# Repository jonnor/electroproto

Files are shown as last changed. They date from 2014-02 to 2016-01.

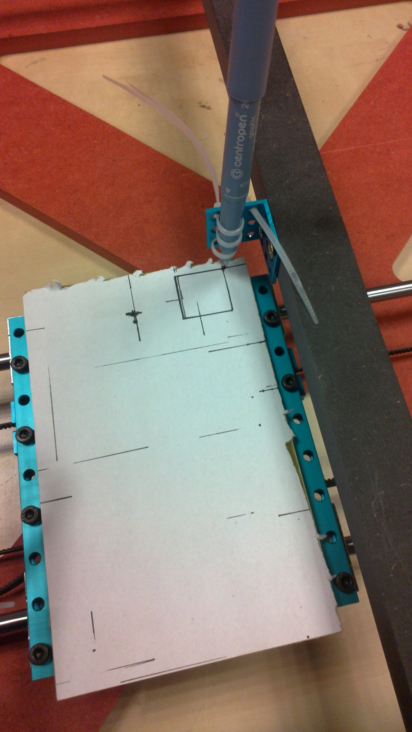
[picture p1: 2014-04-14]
doc/pictures/first-pen-test.jpg

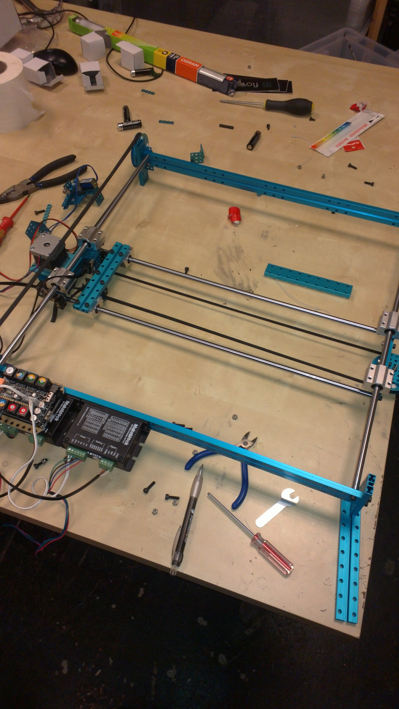
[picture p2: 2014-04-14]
doc/pictures/xyproto-build-in-progress.jpg

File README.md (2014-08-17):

ElectroProto is a prototyping and small-scale production system for electronics.
It aims to allow you to realize eletronics from a schematic in under 1 hour, with
minimal manual steps once the process is started.

ElectroProto aims to be cheap, small and safe/covenient enough that every hackerspace,
and engineering individual, can have one - next to their 3d printer.

Goals:
* Optimized for prototyping, `1-10 boards`
* `End-to-end`, raw materials in, assembly-ready electronics out
* Complete board in `<1 hour`
* `No manual intervention` required during process
* Precise enough for `simple SMT designs`. 0805, SOIC

Status
=======
Proof-of-concept in progress

Milestones
===========
* 0.0.1: Proof-of-concept. Can mill+drill a PCB, without intermediate manual steps.
* 0.1.0: Minimally useful. Can mill+drill+paste a PCB, "-". Board cutout, component placement and reflow done manually.
* 0.2.0: Can mill+drill+cutout+paste a PCB, "-".
* 0.3.0: Can mill+drill+paste+pick-and-place a PCB ". Solder reflow done manually.
* 0.4.0: Can mill+drill+paste+pick-and-place+reflow a PCB ".
* x.0.0: Electroproto is available for purchase from several manufacturers, and can be made using standard fablab tools.

DONE
=====
* Computer-controlled XY axis, based on Makerblock robot plotter kit.
Basic motion and testing with pen completed.
* Prototype Z axis based on moving bed created.
* Vacum-controlled solder dispenser sourced, cheap china copy.

TODO
======
0.0.1: Proof-of-concept
Goal: September, 2014

* CNC a top-plate for tool mounting, based on bottom plate design
* Make Z-axis functional
** Splice belt
** Modify motor mount to include belt-tightening
* Test/verify XY precision, speed using pen. Calculate requirements
* Create toolmounts for dremel-like multi-tools
* Mount mill+drill toolheads
* Allow to input a set of Gerber files for the PCB traces and holes
* Produce first real PCB

0.1.0: Minimally useful
Goal: November, 2014

* Hack solder paster to be computer controlled, test.
* Produce real PCB for demo
* Improve Gerber input to also dispense solder paste on the PCB
* Document the build for reproducability

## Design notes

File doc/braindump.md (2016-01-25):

Current architecture
=======================
* Moving XY bed
* Belt drive (probably need to change to thread drive pretty fast?)
* Tools mounted stationary in roof of machine
* Each job has a dedicated tool/head, with individual Z axis

Open questions
* How to make movable Z-axis??
* What kind of structure to use for joining the XY framing and the roof with heads?

Related projects
===================

Firepick
-----------
* http://firepick.org
* Open source
* Electronics manufacturing machine
* Focused on pick-and-place but attempting more
* Same general motivation, but focused more on high-end/production use

OpenPnP
------
* http://openpnp.org
* Pick-and-place machine
* Open source

Considerations
=================
* X-Y working area: 160x200mm, enough for 2x std EURO rack PCBs (or 1PCB+1pick-and-place tray)
* Precision: ? Enough to do ICs like TQFP ML44
* Z axis tool weight capacity: 0.5 kg, enough for dremel/multitool spindle

The various tool heads should go as closely together as possible to minimize overhead for XY axis.

* Cut-out requires the most XY strength. Workaround: many passes
* Trace milling requires the most precision, drilling and pasting second.
* Drilling the most Z-axis strength

As a start the PCB mounting can be 160x100mm only, or similar.
Limitation: single-sided PCBs. Seems to complicated for its usefulness to attempt
to create a dual-sided machine or automatic flipping mechanism.
Allowing for an already populated board to be manually mounted the other way and software
to support this is definetely possible though.

Both copper and glass fiber dust is quite unhealthy. The design should incorporate a solution for
not letting this into the air that the operator breathes. Having a shroud/case is useful, but
also draft with filtering will be neccesary.

Development
=============
Always focus on the whole process of realizing electronics, from schematics to finished product,
integrated into the physical assembly.

Use a pen-holder with 0.2 mm pen for initial runs, use to determine maximum precision.
Just use a wooden offering plate and drills screws directly into it for initial PCB mounting?
Mount a camera and light, record processes for documentation and debug. Take a picture of every finished board,
dump this together with all the input data of the job. Overlay results with theoretical/ideal, use as evalutation basis.

Get to a workable revision 1 machine as fast as possible, conducting many experiments to learn what is needed.
When the limits of that architecture has been found, build up a separate generation 2 machine.
Keep generation 1 machine operational for practical/usage experience while developing rev 2.

Testprod items
===============
Ideally be something that can be given away, sold cheaply online,
used by myself or others in hackerspace, or nice things to do workshops on.

* Arduino Nano, Trinket or similar devboard
* Piezo amplifiers
* Analog synth modules
* Guitar effects
* Sensorbricks!
* Reprap motor drivers

Reprap principles applied to electronics
========================
* Can the machine reproduce all its electronics?
* Can it be built using (primarily) a reprap 3d-printer,
and then be used to create the electronics for a reprap?

SMT for non-SMD
=================
Most hackers and hackerspaces still produce non-SMT, and have tons of non-SMD components lying around.
Drilling holes and soldering manually however is a pain. How well does it work to:
* Solder DIL8 to DIL24 with pads+solderpaste
* Solder TO92 and TO220 "
* Solder wires for interconnect
* Handle vias. 0 ohm resistors enough?

Can one use solderpaste with a through-hole component mounted normally, for cases where bending the
legs of component, lying the component sideways is not desired?
Can one automatically deposit paste ahead of component placement?

Automated PCB testing
=======================
Flying-probes style testing allows to automatically detect many types of production failures on PCBs.
One could build this with two individually controllable XY (Z) axis
probes, one handling "right hand" and one "left hand" probe. Could also use 4 probes, each covering one "corner".
Each probe would have to be able to both stimulate and measure, and software verify
actual electrical characteristics against the expected.

For low-complexity PCBs one could maybe use a standardized bed-of-nails test fixture,
with NxM nails in a YYY mil spaced grid where each nail can be individually raised or lowered.
The nails could maybe be controlled by linear actuators/solenoids, or be bi-stable such that they
could be "poked down" at start of test run.

References

* [Instructables: How to build custom bed-of-nails tester](http://www.instructables.com/id/How-to-build-a-custom-bed-of-nails-tester-for-your)

Links
=======

* [MIT POP Fab](http://mtm.cba.mit.edu): Mill, vinyl cutter, 3d printer in a suitcase.
* [MIT reconfigurable stages](http://mtm.cba.mit.edu/machines/stages/). Idea for Z-axis?
* [Stepper precison calculator](http://calculator.josefprusa.cz)
* [Shapeoko open hardware desktop CNC](https://www.inventables.com/technologies/desktop-cnc-mill-kit-shapeoko-2)

SW
====
* PCB milling codegen: https://github.com/Traumflug/Visolate
* Kicad->Cyclone PCB Factory scripts->Printrun->Teacup firmware (-> and Gen7 hardware) to manufacture PB’s.
* pcb2gcode: http://sourceforge.net/apps/mediawiki/pcb2gcode/index.php?title=Main_Page

Moving-Z carriage
=====================
Joakim at Bitraf came up with the idea of having the carriage be the Z-axis,
to avoid having to create one per tool.

* Required travel: 20mm, 5mm work + 15mm safe-Z (for avoiding components)
* Required weight capacity: 100 gram? (mount-plate + PCB + components)
* For drilling, needs to withhold the vertical force acted
* For solder-paste, should be fast to be able to do many holes. Use very low safe-Z, 2-3 mm

Due to the low travel required, could perhaps use a simple cam-follower, driven by a servo.

* Cam principles: [Wikipedia](http://en.wikipedia.org/wiki/Cam), [cmu.edu](http://www.cs.cmu.edu/~rapidproto/mechanisms/chpt6.html)

Host WS & User interface
================

Must be able to run on a cheap embedded device (like RPI).
User interface should be browser based, requiring zero install of custom tools.
Want people to be able to come into hackerspace with only their design and layout, and realize it.
Want ability to build statistics of machine usage, to capture the live process on a video camera, and make time-lapses.
Automatic publishing of these artifacts to show activity and results, improvements over time.

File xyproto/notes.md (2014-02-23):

TODO
=====
* Mill bottom plate. Remember cutout/pocket for parts that go lower
* Mill top plate, with mounting for tool heads. Swap the one long piece for a shorter one
* Create a PCB hold-down solution.
* Create a toolhead with just a pen, use to do accuracy/precision tests
* Create a toolhead for milling/drilling. Requires Z-axis, spindle and mount
* Hook up a real EDA tool to the machine, using a standard format
* Order and fit second drive belt for X axis
* Mount a camera as a "tool head"?

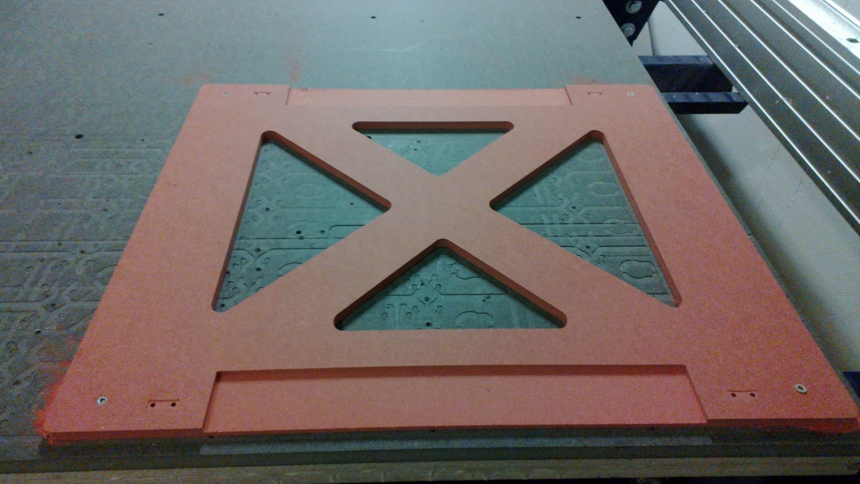
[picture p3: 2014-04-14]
doc/pictures/baseplate-ready-shopbot.jpg

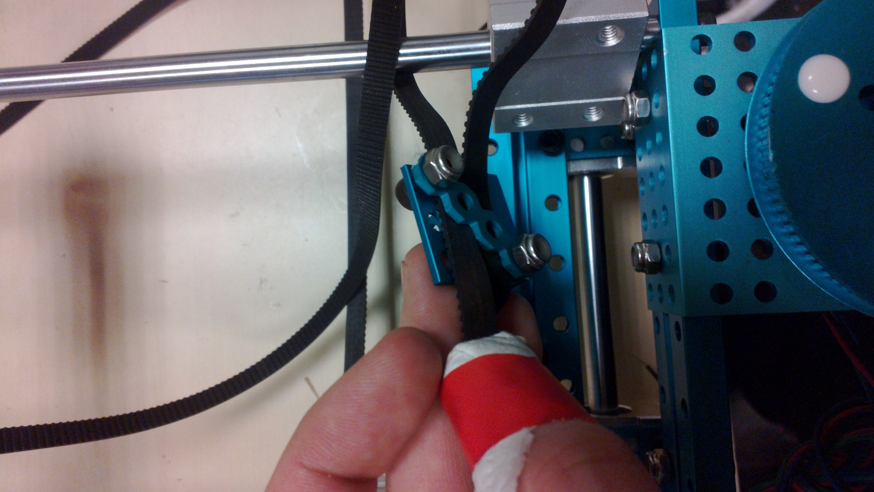
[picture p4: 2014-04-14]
doc/pictures/belt-fastener-1.jpg

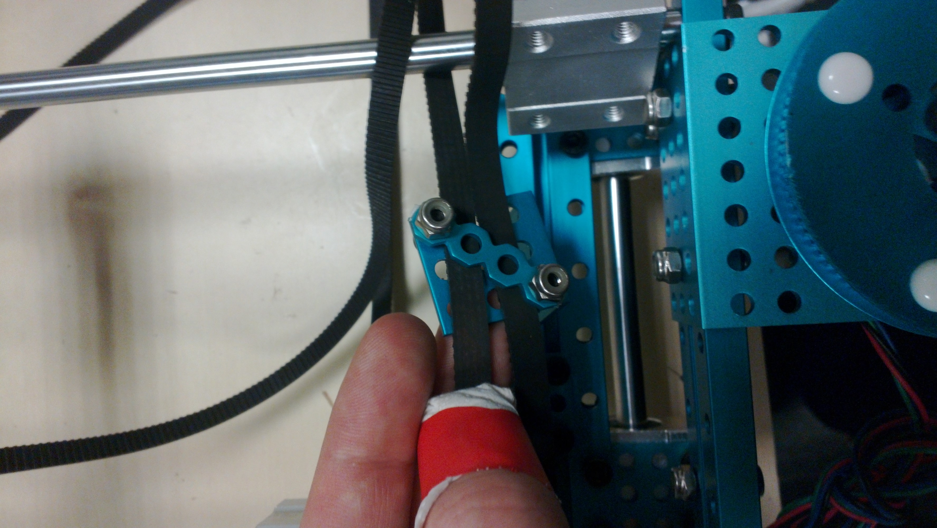
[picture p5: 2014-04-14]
doc/pictures/belt-fastener-2.jpg

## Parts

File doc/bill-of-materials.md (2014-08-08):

Bill of materials
===================
Note: this just reflects the work-in-progress. Any released version might have major alterations.

XY-axis
* [Makeblock XY-plotter kit w/electronics](http://www.makeblock.cc/xy-plotter-robot-kit-with-electronics/)

Chassis
* CNC milled base, from 8mm(?) valcromat

Z-axis

* Additional alu profile+linear guides (Makeblock)
* [28BYJ-48 stepper w/ ULN2003 driver](http://4tronix.co.uk/store/index.php?rt=product/product&keyword=stepper&product_id=196)
* [3d-printed steppermotor pulley ](http://www.thingiverse.com/thing:113201)
* 4 leadscrews pulleys (Makeblock)
* Extra MXL belt (Makeblock)
* 4mm plastic board (Clas Ohlson)

Tools

* Dremel-like multi-tool (Clas Ohlson)
* Pneumatic solder-paste dispenser (DealExtreme)

TODO
------
* 4mm internal (or maybe 3/16") bearings. (G. Heier, T. Meyers gt 7?)

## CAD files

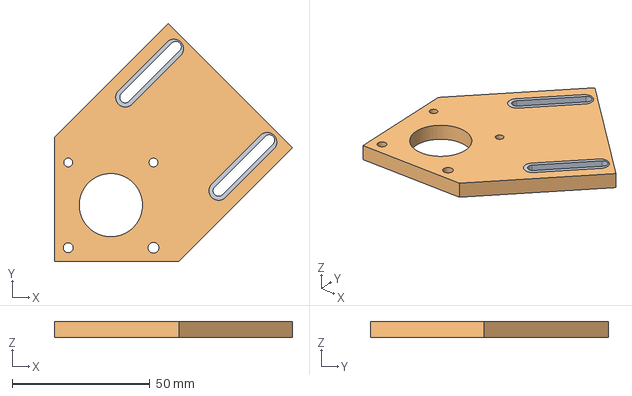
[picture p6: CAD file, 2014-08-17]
xyproto/zaxis-bigmotormount.fcstd
86.5 x 86.5 x 6.00 mm

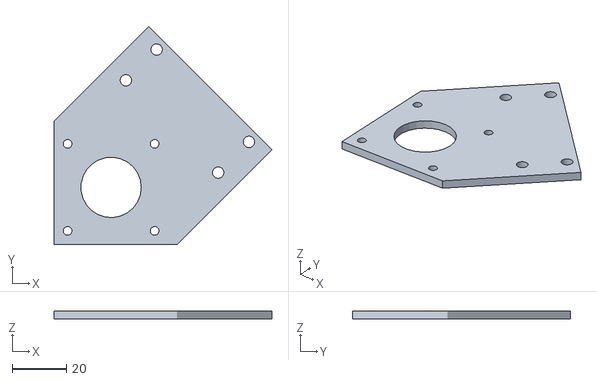
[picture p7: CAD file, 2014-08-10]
xyproto/motormount-large1.obj
80.2 x 80.2 x 3.00

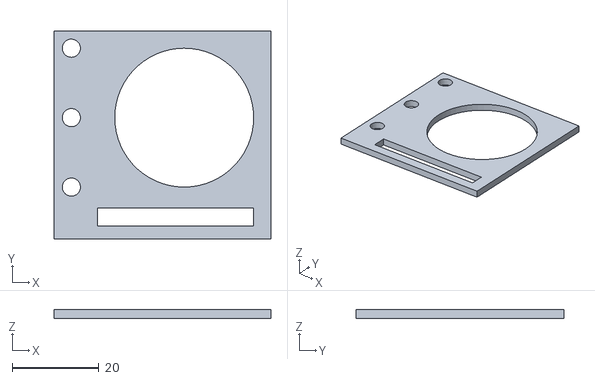
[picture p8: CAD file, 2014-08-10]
xyproto/motormount-sketch1.obj
50.0 x 48.0 x 2.00

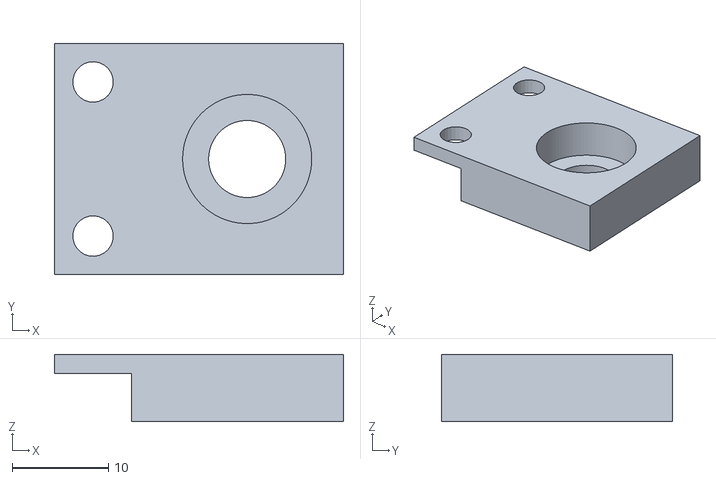
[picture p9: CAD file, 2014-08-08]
xyproto/bearingtest.obj
30.0 x 24.0 x 7.00

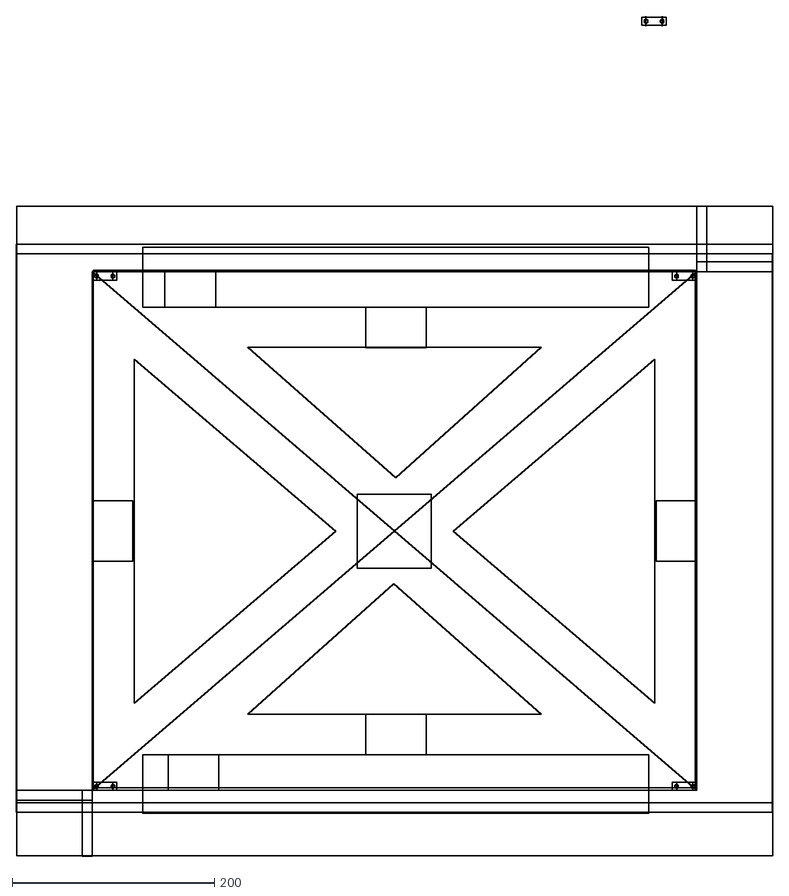
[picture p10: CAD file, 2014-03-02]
xyproto/plates.dxf
747.2 x 829.9

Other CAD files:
xyproto/zaxis-leadscrew-bearingholder.fcstd

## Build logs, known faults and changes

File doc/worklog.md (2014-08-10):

February 22-23, 2014
--------------------
Assembled the Makeblock.cc pen plotter kit,
rebuilt to become a more suitable X-Y axis for PCB production.
Did very simple movement and pen-testing to verify all pieces
working.

https://twitter.com/jononor/status/437729057992867840

15 hours.

March 2, 2014
-------------
Designed and milled a bottom plate for stiffening up the X-Y axis.

6 hours.

April 13-14
-------------
Investigated designs for Z-axis. Prototyped a moving-bed
solution based on principle of a cam. Friction was found to
be too high, required precision and rigidity too demanding
to be easily reproducable.
Decided to prototype a moving-bed with 4 axel screws driven by
single step motor and belts next.

10 hours.

August 7-10, 2014
-------------------
Prototyping moving-bed Z-axis design using 4 leadscrews,
driven by one common belt on a stepper-motor.
Using M4 press-fit nut inserts in bed for receiving the leadscrews.

Trivial solution hacked together using standard Makeblock parts was non-functional
due instable motor mount, poor belt tension and too high friction in the leadscrews.

Designed & 3d-printed leadscrew bearing mounts. My first part created in FreeCAD.

After testing with custom motor mount, dound that 28BYJ stepper motor was too weak.
Changed to Makeblock stepper+driver. Uses stock belt pulley, also works better than 3d-printed.

Z-axis now basically functional.
Still needs belt-tightener and fusing the belt to avoid joints too work properly.

16 hours.

NEXT
-----

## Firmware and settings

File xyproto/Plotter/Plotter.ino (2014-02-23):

/*************************************************************************
* File Name          : Plotter.ino
* Author             : Evan
* Updated            : Ander
* Version            : V0.1.0
* Date               : 10/10/2013
* Description        : Data transmission format (7 byte):
                       =======================================
                        [6]   [5]   [4]   [3]   [2]   [1]   [0]
                        
                        
                        
                        
                       End:0xFD for Data,0xFC for Reset
                       =======================================
* License            : CC-BY-SA 3.0
* Copyright (C) 2011-2013 Hulu Robot Technology Co., Ltd. All right reserved.
* http://www.makeblock.cc/
**************************************************************************/

#include <SoftwareSerial.h>
#include <Me_BaseShield.h>
#include <Me_Bluetooth.h>
//   #include "AccelStepper.h"

class AccelStepper
{
public:
    /// \brief Symbolic names for number of pins.
    /// Use this in the pins argument the AccelStepper constructor to 
    /// provide a symbolic name for the number of pins
    /// to use.
    typedef enum
    {
	FUNCTION  = 0, ///< Use the functional interface, implementing your own driver functions (internal use only)
	DRIVER    = 1, ///< Stepper Driver, 2 driver pins required
	FULL2WIRE = 2, ///< 2 wire stepper, 2 motor pins required
	FULL3WIRE = 3, ///< 3 wire stepper, such as HDD spindle, 3 motor pins required
        FULL4WIRE = 4, ///< 4 wire full stepper, 4 motor pins required
	HALF3WIRE = 6, ///< 3 wire half stepper, such as HDD spindle, 3 motor pins required
	HALF4WIRE = 8  ///< 4 wire half stepper, 4 motor pins required
    } MotorInterfaceType;

    /// Constructor. You can have multiple simultaneous steppers, all moving
    /// at different speeds and accelerations, provided you call their run()
    /// functions at frequent enough intervals. Current Position is set to 0, target
    /// position is set to 0. MaxSpeed and Acceleration default to 1.0.
    /// The motor pins will be initialised to OUTPUT mode during the
    /// constructor by a call to enableOutputs().
    /// \param[in] interface Number of pins to interface to. 1, 2, 4 or 8 are
    /// supported, but it is preferred to use the \ref MotorInterfaceType symbolic names. 
    /// AccelStepper::DRIVER (1) means a stepper driver (with Step and Direction pins).
    /// If an enable line is also needed, call setEnablePin() after construction.
    /// You may also invert the pins using setPinsInverted().
    /// AccelStepper::FULL2WIRE (2) means a 2 wire stepper (2 pins required). 
    /// AccelStepper::FULL3WIRE (3) means a 3 wire stepper, such as HDD spindle (3 pins required). 
    /// AccelStepper::FULL4WIRE (4) means a 4 wire stepper (4 pins required). 
    /// AccelStepper::HALF3WIRE (6) means a 3 wire half stepper, such as HDD spindle (3 pins required)
    /// AccelStepper::HALF4WIRE (8) means a 4 wire half stepper (4 pins required)
    /// Defaults to AccelStepper::FULL4WIRE (4) pins.
    /// \param[in] pin1 Arduino digital pin number for motor pin 1. Defaults
    /// to pin 2. For a AccelStepper::DRIVER (pins==1), 
    /// this is the Step input to the driver. Low to high transition means to step)
    /// \param[in] pin2 Arduino digital pin number for motor pin 2. Defaults
    /// to pin 3. For a AccelStepper::DRIVER (pins==1), 
    /// this is the Direction input the driver. High means forward.
    /// \param[in] pin3 Arduino digital pin number for motor pin 3. Defaults
    /// to pin 4.
    /// \param[in] pin4 Arduino digital pin number for motor pin 4. Defaults
    /// to pin 5.
    /// \param[in] enable If this is true (the default), enableOutpuys() will be called to enable
    /// the output pins at construction time.
    AccelStepper(uint8_t interface = AccelStepper::FULL4WIRE, uint8_t pin1 = 2, uint8_t pin2 = 3, uint8_t pin3 = 4, uint8_t pin4 = 5, bool enable = true);

    /// Alternate Constructor which will call your own functions for forward and backward steps. 
    /// You can have multiple simultaneous steppers, all moving
    /// at different speeds and accelerations, provided you call their run()
    /// functions at frequent enough intervals. Current Position is set to 0, target
    /// position is set to 0. MaxSpeed and Acceleration default to 1.0.
    /// Any motor initialization should happen before hand, no pins are used or initialized.
    /// \param[in] forward void-returning procedure that will make a forward step
    /// \param[in] backward void-returning procedure that will make a backward step
    AccelStepper(void (*forward)(), void (*backward)());
    
    /// Set the target position. The run() function will try to move the motor
    /// from the current position to the target position set by the most
    /// recent call to this function. Caution: moveTo() also recalculates the speed for the next step. 
    /// If you are trying to use constant speed movements, you should call setSpeed() after calling moveTo().
    /// \param[in] absolute The desired absolute position. Negative is
    /// anticlockwise from the 0 position.
    void    moveTo(long absolute); 

    /// Set the target position relative to the current position
    /// \param[in] relative The desired position relative to the current position. Negative is
    /// anticlockwise from the current position.
    void    move(long relative);

    /// Poll the motor and step it if a step is due, implementing
    /// accelerations and decelerations to acheive the target position. You must call this as
    /// frequently as possible, but at least once per minimum step interval,
    /// preferably in your main loop.
    /// \return true if the motor is at the target position.
    boolean run();

    /// Poll the motor and step it if a step is due, implmenting a constant
    /// speed as set by the most recent call to setSpeed(). You must call this as
    /// frequently as possible, but at least once per step interval,
    /// \return true if the motor was stepped.
    boolean runSpeed();

    /// Sets the maximum permitted speed. the run() function will accelerate
    /// up to the speed set by this function.
    /// \param[in] speed The desired maximum speed in steps per second. Must
    /// be > 0. Caution: Speeds that exceed the maximum speed supported by the processor may
    /// Result in non-linear accelerations and decelerations.
    void    setMaxSpeed(float speed);

    /// Sets the acceleration and deceleration parameter.
    /// \param[in] acceleration The desired acceleration in steps per second
    /// per second. Must be > 0.0. This is an expensive call since it requires a square 
    /// root to be calculated. Dont call more ofthen than needed
    void    setAcceleration(float acceleration);

    /// Sets the desired constant speed for use with runSpeed().
    /// \param[in] speed The desired constant speed in steps per
    /// second. Positive is clockwise. Speeds of more than 1000 steps per
    /// second are unreliable. Very slow speeds may be set (eg 0.00027777 for
    /// once per hour, approximately. Speed accuracy depends on the Arduino
    /// crystal. Jitter depends on how frequently you call the runSpeed() function.
    void    setSpeed(float speed);

    /// The most recently set speed
    /// \return the most recent speed in steps per second
    float   speed();

    /// The distance from the current position to the target position.
    /// \return the distance from the current position to the target position
    /// in steps. Positive is clockwise from the current position.
    long    distanceToGo();

    /// The most recently set target position.
    /// \return the target position
    /// in steps. Positive is clockwise from the 0 position.
    long    targetPosition();

    /// The currently motor position.
    /// \return the current motor position
    /// in steps. Positive is clockwise from the 0 position.
    long    currentPosition();  

    /// Resets the current position of the motor, so that wherever the motor
    /// happens to be right now is considered to be the new 0 position. Useful
    /// for setting a zero position on a stepper after an initial hardware
    /// positioning move.
    /// Has the side effect of setting the current motor speed to 0.
    /// \param[in] position The position in steps of wherever the motor
    /// happens to be right now.
    void    setCurrentPosition(long position);  
    
    /// Moves the motor at the currently selected constant speed (forward or reverse) 
    /// to the target position and blocks until it is at
    /// position. Dont use this in event loops, since it blocks.
    void    runToPosition();

    /// Runs at the currently selected speed until the target position is reached
    /// Does not implement accelerations.
    /// \return true if it stepped
    boolean runSpeedToPosition();

    /// Moves the motor to the new target position and blocks until it is at
    /// position. Dont use this in event loops, since it blocks.
    /// \param[in] position The new target position.
    void    runToNewPosition(long position);

    /// Sets a new target position that causes the stepper
    /// to stop as quickly as possible, using to the current speed and acceleration parameters.
    void stop();

    /// Disable motor pin outputs by setting them all LOW
    /// Depending on the design of your electronics this may turn off
    /// the power to the motor coils, saving power.
    /// This is useful to support Arduino low power modes: disable the outputs
    /// during sleep and then reenable with enableOutputs() before stepping
    /// again.
    virtual void    disableOutputs();

    /// Enable motor pin outputs by setting the motor pins to OUTPUT
    /// mode. Called automatically by the constructor.
    virtual void    enableOutputs();

    /// Sets the minimum pulse width allowed by the stepper driver. The minimum practical pulse width is 
    /// approximately 20 microseconds. Times less than 20 microseconds
    /// will usually result in 20 microseconds or so.
    /// \param[in] minWidth The minimum pulse width in microseconds. 
    void    setMinPulseWidth(unsigned int minWidth);

    /// Sets the enable pin number for stepper drivers.
    /// 0xFF indicates unused (default).
    /// Otherwise, if a pin is set, the pin will be turned on when 
    /// enableOutputs() is called and switched off when disableOutputs() 
    /// is called.
    /// \param[in] enablePin Arduino digital pin number for motor enable
    /// \sa setPinsInverted
    void    setEnablePin(uint8_t enablePin = 0xff);

    /// Sets the inversion for stepper driver pins
    /// \param[in] directionInvert True for inverted direction pin, false for non-inverted
    /// \param[in] stepInvert      True for inverted step pin, false for non-inverted
    /// \param[in] enableInvert    True for inverted enable pin, false (default) for non-inverted
    void    setPinsInverted(bool directionInvert = false, bool stepInvert = false, bool enableInvert = false);

    /// Sets the inversion for 2, 3 and 4 wire stepper pins
    /// \param[in] pin1Invert True for inverted pin1, false for non-inverted
    /// \param[in] pin2Invert True for inverted pin2, false for non-inverted
    /// \param[in] pin3Invert True for inverted pin3, false for non-inverted
    /// \param[in] pin4Invert True for inverted pin4, false for non-inverted
    /// \param[in] enableInvert    True for inverted enable pin, false (default) for non-inverted
    void    setPinsInverted(bool pin1Invert, bool pin2Invert, bool pin3Invert, bool pin4Invert, bool enableInvert);

protected:

    /// \brief Direction indicator
    /// Symbolic names for the direction the motor is turning
    typedef enum
    {
	DIRECTION_CCW = 0,  ///< Clockwise
        DIRECTION_CW  = 1   ///< Counter-Clockwise
    } Direction;

    /// Forces the library to compute a new instantaneous speed and set that as
    /// the current speed. It is called by
    /// the library:
    /// \li  after each step
    /// \li  after change to maxSpeed through setMaxSpeed()
    /// \li  after change to acceleration through setAcceleration()
    /// \li  after change to target position (relative or absolute) through
    /// move() or moveTo()
    void           computeNewSpeed();

    /// Low level function to set the motor output pins
    /// bit 0 of the mask corresponds to _pin[0]
    /// bit 1 of the mask corresponds to _pin[1]
    /// You can override this to impment, for example serial chip output insted of using the
    /// output pins directly
    virtual void   setOutputPins(uint8_t mask);

    /// Called to execute a step. Only called when a new step is
    /// required. Subclasses may override to implement new stepping
    /// interfaces. The default calls step1(), step2(), step4() or step8() depending on the
    /// number of pins defined for the stepper.
    /// \param[in] step The current step phase number (0 to 7)
    virtual void   step(long step);

    /// Called to execute a step using stepper functions (pins = 0) Only called when a new step is
    /// required. Calls _forward() or _backward() to perform the step
    /// \param[in] step The current step phase number (0 to 7)
    virtual void   step0(long step);

    /// Called to execute a step on a stepper driver (ie where pins == 1). Only called when a new step is
    /// required. Subclasses may override to implement new stepping
    /// interfaces. The default sets or clears the outputs of Step pin1 to step, 
    /// and sets the output of _pin2 to the desired direction. The Step pin (_pin1) is pulsed for 1 microsecond
    /// which is the minimum STEP pulse width for the 3967 driver.
    /// \param[in] step The current step phase number (0 to 7)
    virtual void   step1(long step);

    /// Called to execute a step on a 2 pin motor. Only called when a new step is
    /// required. Subclasses may override to implement new stepping
    /// interfaces. The default sets or clears the outputs of pin1 and pin2
    /// \param[in] step The current step phase number (0 to 7)
    virtual void   step2(long step);

    /// Called to execute a step on a 3 pin motor, such as HDD spindle. Only called when a new step is
    /// required. Subclasses may override to implement new stepping
    /// interfaces. The default sets or clears the outputs of pin1, pin2,
    /// pin3
    /// \param[in] step The current step phase number (0 to 7)
    virtual void   step3(long step);

    /// Called to execute a step on a 4 pin motor. Only called when a new step is
    /// required. Subclasses may override to implement new stepping
    /// interfaces. The default sets or clears the outputs of pin1, pin2,
    /// pin3, pin4.
    /// \param[in] step The current step phase number (0 to 7)
    virtual void   step4(long step);

    /// Called to execute a step on a 3 pin motor, such as HDD spindle. Only called when a new step is
    /// required. Subclasses may override to implement new stepping
    /// interfaces. The default sets or clears the outputs of pin1, pin2,
    /// pin3
    /// \param[in] step The current step phase number (0 to 7)
    virtual void   step6(long step);

    /// Called to execute a step on a 4 pin half-steper motor. Only called when a new step is
    /// required. Subclasses may override to implement new stepping
    /// interfaces. The default sets or clears the outputs of pin1, pin2,
    /// pin3, pin4.
    /// \param[in] step The current step phase number (0 to 7)
    virtual void   step8(long step);

private:
    /// Number of pins on the stepper motor. Permits 2 or 4. 2 pins is a
    /// bipolar, and 4 pins is a unipolar.
    uint8_t        _interface;          // 0, 1, 2, 4, 8, See MotorInterfaceType

    /// Arduino pin number assignments for the 2 or 4 pins required to interface to the
    /// stepper motor or driver
    uint8_t        _pin[4];

    /// Whether the _pins is inverted or not
    uint8_t        _pinInverted[4];

    /// The current absolution position in steps.
    long           _currentPos;    // Steps

    /// The target position in steps. The AccelStepper library will move the
    /// motor from the _currentPos to the _targetPos, taking into account the
    /// max speed, acceleration and deceleration
    long           _targetPos;     // Steps

    /// The current motos speed in steps per second
    /// Positive is clockwise
    float          _speed;         // Steps per second

    /// The maximum permitted speed in steps per second. Must be > 0.
    float          _maxSpeed;

    /// The acceleration to use to accelerate or decelerate the motor in steps
    /// per second per second. Must be > 0
    float          _acceleration;
    float          _sqrt_twoa; // Precomputed sqrt(2*_acceleration)

    /// The current interval between steps in microseconds.
    /// 0 means the motor is currently stopped with _speed == 0
    unsigned long  _stepInterval;

    /// The last step time in microseconds
    unsigned long  _lastStepTime;

    /// The minimum allowed pulse width in microseconds
    unsigned int   _minPulseWidth;

    /// Is the direction pin inverted?
    ///bool           _dirInverted; /// Moved to _pinInverted[1]

    /// Is the step pin inverted?
    ///bool           _stepInverted; /// Moved to _pinInverted[0]

    /// Is the enable pin inverted?
    bool           _enableInverted;

    /// Enable pin for stepper driver, or 0xFF if unused.
    uint8_t        _enablePin;

    /// The pointer to a forward-step procedure
    void (*_forward)();

    /// The pointer to a backward-step procedure
    void (*_backward)();

    /// The step counter for speed calculations
    long _n;

    /// Initial step size in microseconds
    float _c0;

    /// Last step size in microseconds
    float _cn;

    /// Min step size in microseconds based on maxSpeed
    float _cmin; // at max speed

    /// Current direction motor is spinning in
    boolean _direction; // 1 == CW

};



#if 0
// Some debugging assistance
void dump(uint8_t* p, int l)
{
    int i;

    for (i = 0; i < l; i++)
    {
	Serial.print(p[i], HEX);
	Serial.print(" ");
    }
    Serial.println("");
}
#endif

void AccelStepper::moveTo(long absolute)
{
    if (_targetPos != absolute)
    {
	_targetPos = absolute;
	computeNewSpeed();
	// compute new n?
    }
}

void AccelStepper::move(long relative)
{
    moveTo(_currentPos + relative);
}

// Implements steps according to the current step interval
// You must call this at least once per step
// returns true if a step occurred
boolean AccelStepper::runSpeed()
{
    // Dont do anything unless we actually have a step interval
    if (!_stepInterval)
	return false;

    unsigned long time = micros();//millis()*1000;
    // Gymnastics to detect wrapping of either the nextStepTime and/or the current time
    unsigned long nextStepTime = _lastStepTime + _stepInterval;
    if (   ((nextStepTime >= _lastStepTime) && ((time >= nextStepTime) || (time < _lastStepTime)))
	|| ((nextStepTime < _lastStepTime) && ((time >= nextStepTime) && (time < _lastStepTime))))

    {
	if (_direction == DIRECTION_CW)
	{
	    // Clockwise
	    _currentPos += 1;
	}
	else
	{
	    // Anticlockwise  
	    _currentPos -= 1;
	}
	step(_currentPos);

	_lastStepTime = time;
	return true;
    }
    else
    {
	return false;
    }
}

long AccelStepper::distanceToGo()
{
    return _targetPos - _currentPos;
}
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
void loop() {
  minIndex = isMoving?5:20;//buffer limit
  if(posIndex<minIndex){
    while(Serial.available()){
        rxBuf = Serial.read();
        if(stateMachine == 0)// check state machine
        {
          if(rxBuf == 0xff) stateMachine = 1;
          else stateMachine = 0;
        }
        else if(stateMachine == 1)
        {
          if(rxBuf == 0xfe) stateMachine = 2;
          else stateMachine = 0;
        }
        else if(stateMachine == 2)// receive data
        {
          dataBuf[t++] = rxBuf&0xff;
          if(t>4){// when receive all of data, reset stateMachine
            if(dataBuf[4]==0xfd){
              posIndex++;
              xPos[posIndex] = (dataBuf[2] + (dataBuf[3]<<8)); yPos[posIndex] = (dataBuf[0] + (dataBuf[1]<<8));//push data into buffer.
              if(yPos[posIndex]<0||yPos[posIndex]>3200)yPos[posIndex]=yPos[posIndex-1]; //limit Y postion
              if(xPos[posIndex]<0||xPos[posIndex]>3200)xPos[posIndex]=xPos[posIndex-1]; //limit X postion
              
            }else if(dataBuf[4]==0xfc){
              //when finish or reset
              analogWrite(motorPwm, 0);
              posIndex = 0;
              delay(1000);
            }
          t=0;// reset 
          stateMachine=0;// reset stateMachine
          }
        }
      }
    }
    stepperX.run();
    stepperY.run(); // scanning stepper motor
    isMoving = posIndex>15;
    if(posIndex>0){
      readPosition();
    }
  //************************************
  //    [3]     [2]     [1]     [0]
  //    Y-H     Y-L     X-H     X-L
  //************************************
}
void readPosition(){
  int i=0;
  if(stepperX.currentPosition() == xLast && stepperY.currentPosition() ==  yLast ){  
        for(i=0;i<posIndex;i++){
          xPos[i]=xPos[i+1];
          yPos[i]=yPos[i+1]; //update buffer
        }
        if(posIndex>0){
          posIndex--;//update buffer index 
        }
        int dx = xLast-xPos[0];
        int dy = yLast-yPos[0];
        unsigned long dist = dx*dx+dy*dy;//calculate distance between points.
        if(dist>25){
           analogWrite(motorPwm, 0); //pen up
        }else{
          if(posIndex!=0) analogWrite(motorPwm, 200);//pen down
        }
    
        stepperY.moveTo(yPos[0]);
        stepperX.moveTo(xPos[0]);
        
        // move to target
        xLast = xPos[0];
        yLast = yPos[0];// save last position
    }
}

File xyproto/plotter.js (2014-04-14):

var SerialPort = require("serialport").SerialPort

function moveTo(x, y) {
  var buf = new Buffer(7);
  buf.writeUInt8(0xFF, 0);
  buf.writeUInt8(0xFE, 1);
  buf.writeUInt16LE(y, 2); // Y
  buf.writeUInt16LE(x, 4); // X
  buf.writeUInt8(0xFD, 6);
  return buf;
}

var serialPort = new SerialPort("/dev/ttyACM0", {
  baudrate: 9600
});

serialPort.on("open", function () {
  console.log('open');
  serialPort.on('data', function(data) {
    console.log('data received: ' + data);
  });

  var workMin = 100;
  var workMax = 2500;
  var sendDelay = 800;
  var positions = [
    [workMin, workMin, sendDelay],
    [workMin, workMax, sendDelay],
    [workMax, workMax, sendDelay],
    [workMax, workMin, sendDelay],
    [workMin, workMin, sendDelay]
  ]
  positions = [
    [100, 100, sendDelay],
    [500, 500, sendDelay],
    [700, 500, sendDelay],
    [700, 700, sendDelay],
    [500, 700, sendDelay],
    [500, 500, sendDelay],
    [100, 100, sendDelay],
  ]
//  positions = [ positions[0] ]

  var nextPos = function(index) {
        if (index < positions.length) {
          var p = positions[index];
          var cmd = moveTo(p[0], p[1]);
          serialPort.write(cmd, function (err, res) {
              if (err) {
                console.log("serialport write error: ", err);
              } else {
                console.log("moved to X,Y (index, written)", p[0], p[1], index, res);
                console.log("waiting for", p[2]/1000, "seconds");
                setTimeout(function () { nextPos(index+1) }, p[2]);
              }
          });
        } else {
            console.log("Sequence over");
            setTimeout(function () { nextPos(0); }, 2000);
        }
  }
  setTimeout(function () { nextPos(0); }, 3000);
  

});

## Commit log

2014-01-28 doc: Add idea about automated PCB testing/verification
2014-02-23 Add notes about XY prototype
2014-03-02 xyproto: Add vector files for top+bottom plate milling
    [plates.dxf]
2014-04-14 doc: Add braindump about having Z-axis on carriage
2014-08-07 doc: Update with latest progress on Z-axis
2014-08-08 Add bearing mounts for Z-axis leadscrew, designed for attaching to Makeblock
    Designed in FreeCAD
    [bearingtest.obj, zaxis-leadscrew-bearingholder.fcstd]
2014-08-10 Add 3d models for new motor mount, update worklog
    [motormount-large1.obj, motormount-sketch1.obj, zaxis-bigmotormount.fcstd]
2014-08-10 Update z-axis test code to reflect motor change
2014-08-17 Add belt tensioning mechanism
    [zaxis-bigmotormount.fcstd]
2014-08-17 Add groves for nuts in belt tensioner
    [zaxis-bigmotormount.fcstd]
2014-08-17 Some tweaks to z-axis motormount
    [zaxis-bigmotormount.fcstd]
2016-01-25 doc: Add link to DIY bed-of-nails to braindump
